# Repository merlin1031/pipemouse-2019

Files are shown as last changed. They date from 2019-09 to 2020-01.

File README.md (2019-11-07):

# pipemouse-2019
Tiny FPV Rover for Pipes
Was ist "PipeMouse 2019"? im Prinzip ist das ein kleiner FPV-Rover mit Kettenantrieb, der klein genug ist um in Röhren oder Schächten bewegt werden zu können. Durch den Antrieb mittels Ketten soll es den Rover möglich sein, auch über kleine Hindernisse oder Absätze zu fahren. Gesteuert wird das Modell mit einer handelsüblichen 2,4 GHz Fernsteuerung. Die Bildübertragung erfolgt über eine Miniatur-FPV-Kamera mit 5,8 GHz Funkübertragung.

## Idee und Konzept
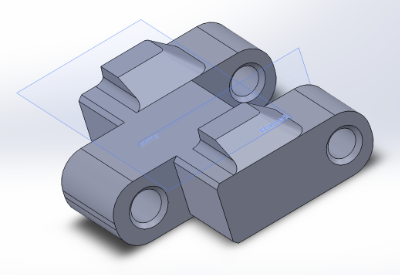
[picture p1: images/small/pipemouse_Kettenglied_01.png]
PipeMouse 2019 - Einzelnes Kettenglied

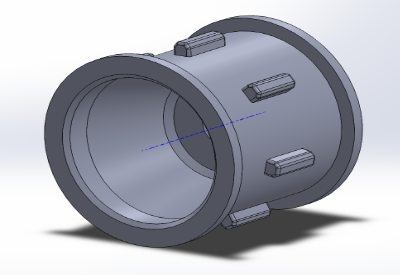
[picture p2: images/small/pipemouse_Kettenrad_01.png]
PipeMouse 2019 - Kettenrad

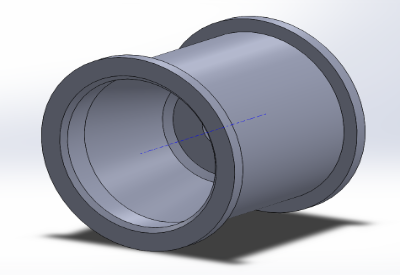
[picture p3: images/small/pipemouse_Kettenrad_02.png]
PipeMouse 2019 - Laufrad zur Unterstüzung der Laufkette

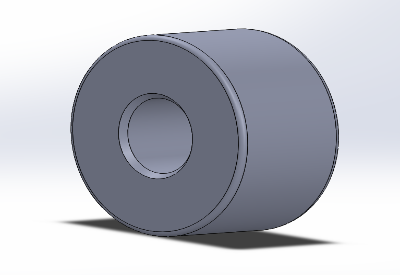
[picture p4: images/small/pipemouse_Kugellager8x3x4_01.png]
PipeMouse 2019 - Kugellager 8x3x4 für die Laufräder


Altenativer Ansatz für Kette mit Gummi-Pads. Aus Moosgummi werden die Pads gelasert und mit Kontaktkleber (z.B. Uhu Por oder Pattex auf den einzelnen Kettengliedern aufgeklebt).
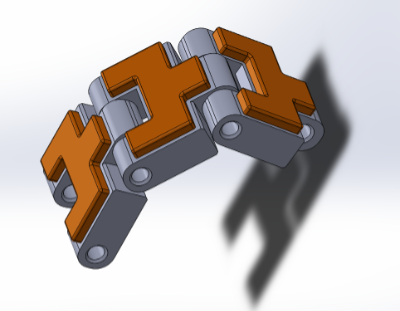
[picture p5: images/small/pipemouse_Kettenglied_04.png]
PipeMouse 2019 - Simulation Kettenglieder mit Gummi-Pad

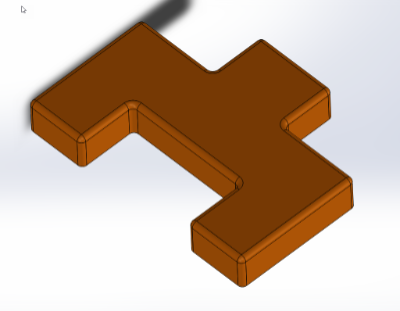
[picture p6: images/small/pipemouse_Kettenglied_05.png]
PipeMouse 2019 - Gummi-Pad für Kettenglied

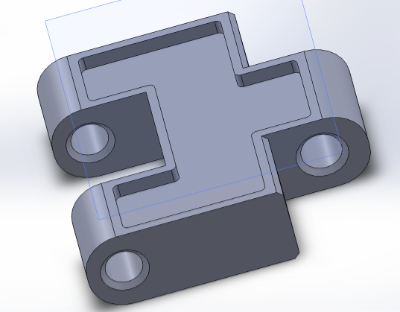
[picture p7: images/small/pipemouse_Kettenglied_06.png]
PipeMouse 2019 - Aussparung für Gummi-Pad in Kettenglied


## Komponenten und Bauteile
### Antrieb
Der Antrieb erfolgt durch zwei auf 360°-Betrieb umgebaute Mini-Servos der 8g-Klasse. Dadurch wird kein besonderer ESC für die Steuerung des Rovers benötigt. Die Steuerung von linker und rechter Kettenseite kann über einem in der Fernsteuerung progammierten Mischer erfolgen.
### Kettenstrang
Der Kettenstrang wird im 3D-Drucker aus PLA gedruckt. Als Verbinger zwischen den einzelnen Kettengliedern kommen PLA-Reste mit einem Durchmesser von 1,75mm zum Einsatz. Widerhaken auf der Lauffläche den Kettengliedern ermöglichen einen sicheren Vortrieb auf rauhen Untergründen, oder an steilen Absätzen. Auf sehr glatten Untergründen werden sicherlich Probleme mit dem Vortrieb auftreten, was aber vernachlässigbar sein dürfte, da in der Wettbewerbs-Arena geeignete Werkstoffe als Fahruntergrund vorhanden sein werden.
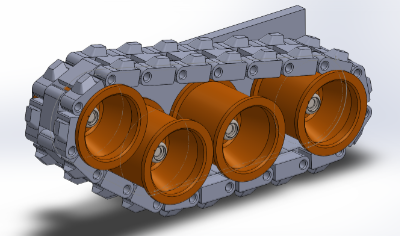
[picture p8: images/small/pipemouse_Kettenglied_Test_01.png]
PipeMouse 2019 - Test Kette mit Baugruppenfeature Riemen/Kette (Aussenansicht)

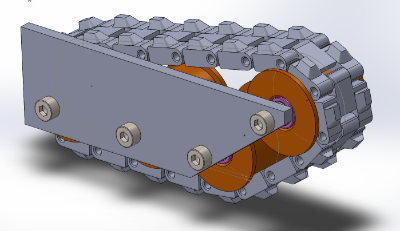
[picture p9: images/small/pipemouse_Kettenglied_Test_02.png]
PipeMouse 2019 - Test Kette mit Baugruppenfeature Riemen/Kette (Innenansicht)

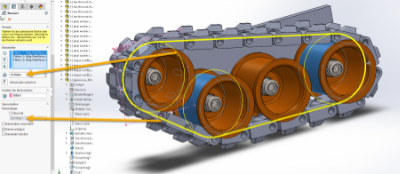
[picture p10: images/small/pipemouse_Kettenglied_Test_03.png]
PipeMouse 2019 - Test Kette mit Baugruppenfeature Riemen/Kette (Feature-Einstellungen)


Zeichungen von Kettenglied und Kettenrad ligen als PDF-Zeichnung im Verzeichnis /CAD/

### Fahrzeugwanne
Die Fahrzeugwanne dient der Aufnahme der Laufräder und der Antriebs-Servos. Sie wird so gestaltet sein, dass sie möglichst viel Bodenfreiheit und eine Möglichkeit der Kettenspannung bieten wird.
### Steuerung
Gesteuert wird der Rover mittels einer handelsüblichen Funkfernsteuerung mit 2,4 GHz-Technologie. In diesem speziellen Fall wird ein Exemplar der Firma FrySky (Taranis) zum Einsatz kommen. Diese Fernsteuerung bietet die Möglichkeit, die eingesetzte Open-Sorce Firmware eigenständig upzudaten und bietet umfangreiche Möglichkeiten der eingenen Programmierung. Zudem sind sehr günstige Miniatur-Empfänger in Briefmarken-Größe verfügbar.
### Stromversorgung
Als Stromquelle dient dem Rover ein 2S 450mAh Lipo-Akku, der aus der Tiny Whoop Copter Szene stammt. Der Vorteil dieses Akkus besteht darin, das die Einzelzellen recht schmal und klein gebaut sind und dadurch sehr wenig Platz im Rover benötigen.

## weitere Infos

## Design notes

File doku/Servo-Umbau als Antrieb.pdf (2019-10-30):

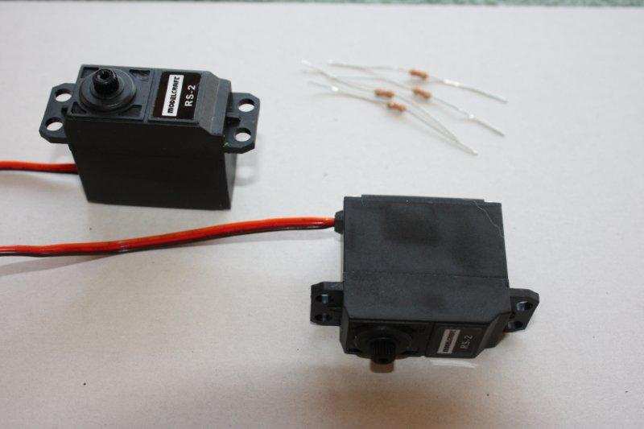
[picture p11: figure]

Seite 1 von 8

Servo-Umbau, damit er als Antrieb verwendet werden kann

Hallo Zusammen,

Ich möchte Euch mal Anhand eines Beispiels zeigen, wie man einen Servo zu einem Antrieb ohne Endstellung umbauen kann und somit als Antrieb für z.B. eine Bruder-Raupe verwenden kann.

Material:

### 1 Stück Standardservo von Conrad Nr. 205111 – 62 2 Stück Metallfilm-Widerstand, axial bedrahtet, Bauform0207, 2,4kOhm, 0.25Watt

von Conrad Nr. 409480-62 (Achtung Art. Nr. ist für ein 100er Pack)

Es ist WICHTIG, dass man wirklich 2,4kOhm Widerstände verwendet, denn bei kleineren Widerständen, z.B. 2,2kOhm ist der Nullpunkt vom Servo nicht so genau und man muss öfters mit der Trimmung den Servo zum Stillstand bringen.
Hier mal das benötigte Material im Überblick:

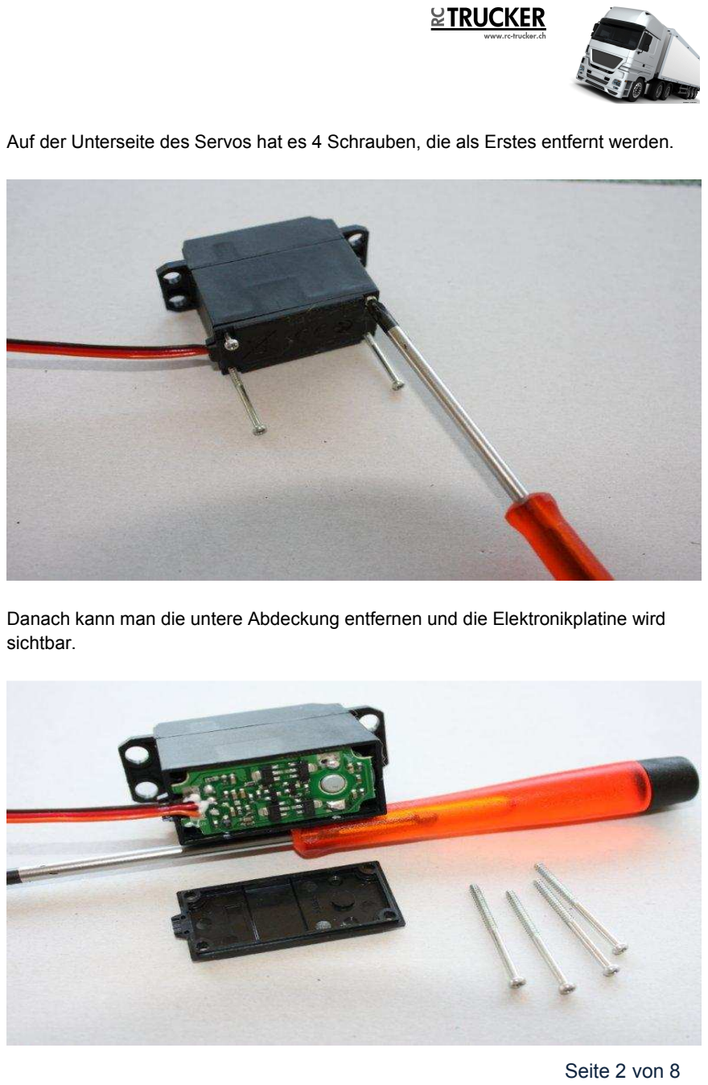
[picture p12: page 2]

Seite 2 von 8

Auf der Unterseite des Servos hat es 4 Schrauben, die als Erstes entfernt werden.

Danach kann man die untere Abdeckung entfernen und die Elektronikplatine wird sichtbar.

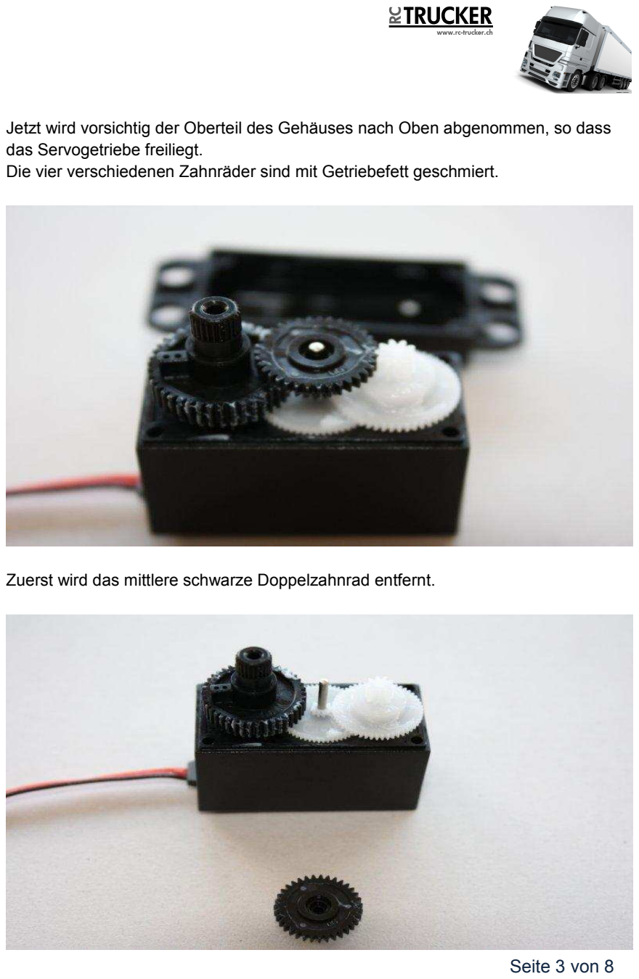
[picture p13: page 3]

Seite 3 von 8

Jetzt wird vorsichtig der Oberteil des Gehäuses nach Oben abgenommen, so dass das Servogetriebe freiliegt.
Die vier verschiedenen Zahnräder sind mit Getriebefett geschmiert.

Zuerst wird das mittlere schwarze Doppelzahnrad entfernt.

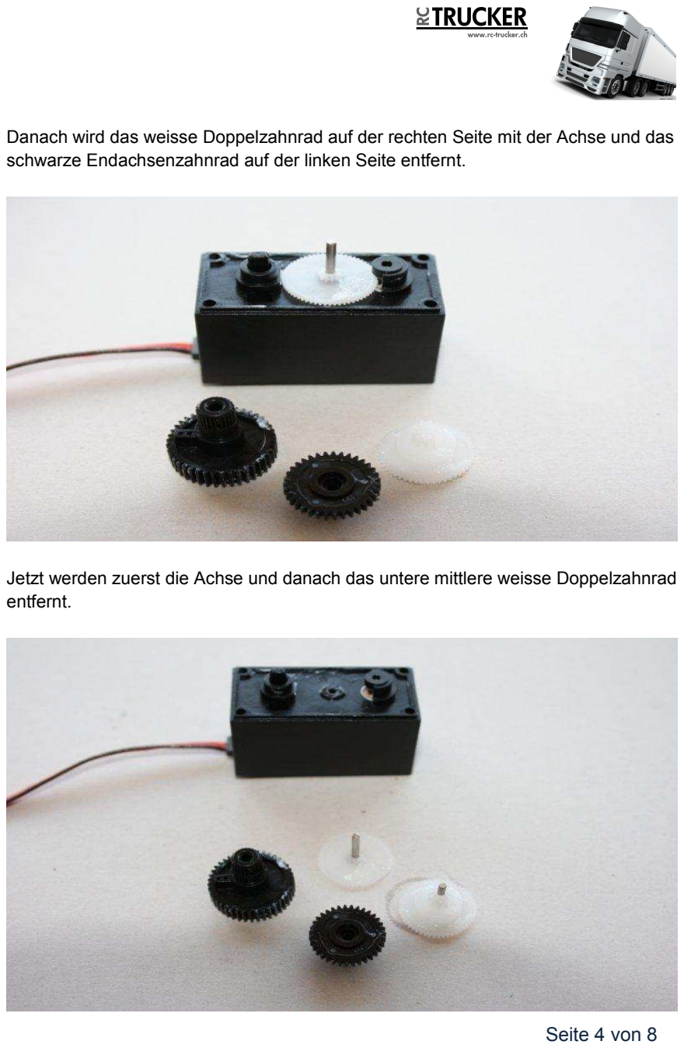
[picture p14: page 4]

Seite 4 von 8

Danach wird das weisse Doppelzahnrad auf der rechten Seite mit der Achse und das schwarze Endachsenzahnrad auf der linken Seite entfernt.

Jetzt werden zuerst die Achse und danach das untere mittlere weisse Doppelzahnrad entfernt.

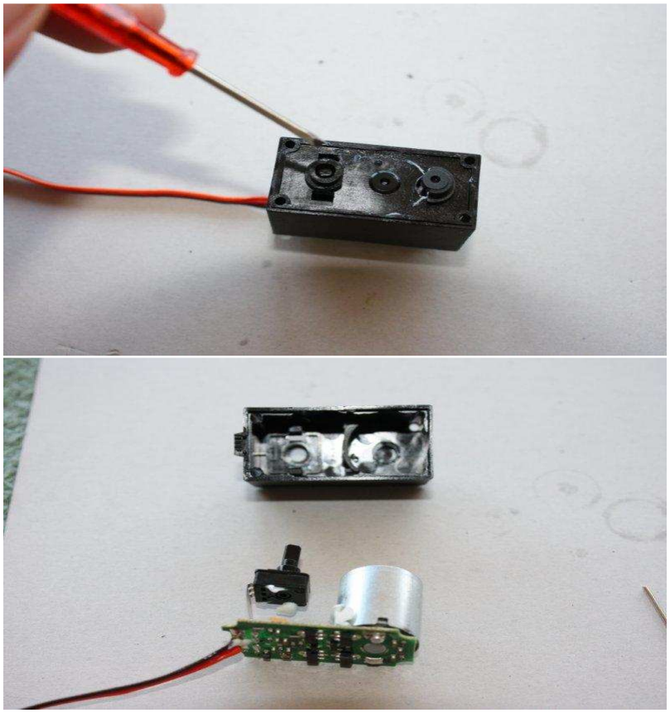
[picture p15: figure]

Seite 5 von 8

Jetzt wird die Elektronik ausgebaut. Dazu kann man VORSICHTIG mit einem kleinen Schraubendreher von Oben in die zwei kleinen Schlitze fahren und die Kunststoffklammern, die das Poti im Gehäuse halten, zur Seite drücken und die Elektronikplatine von unten aus dem Gehäuse ziehen.

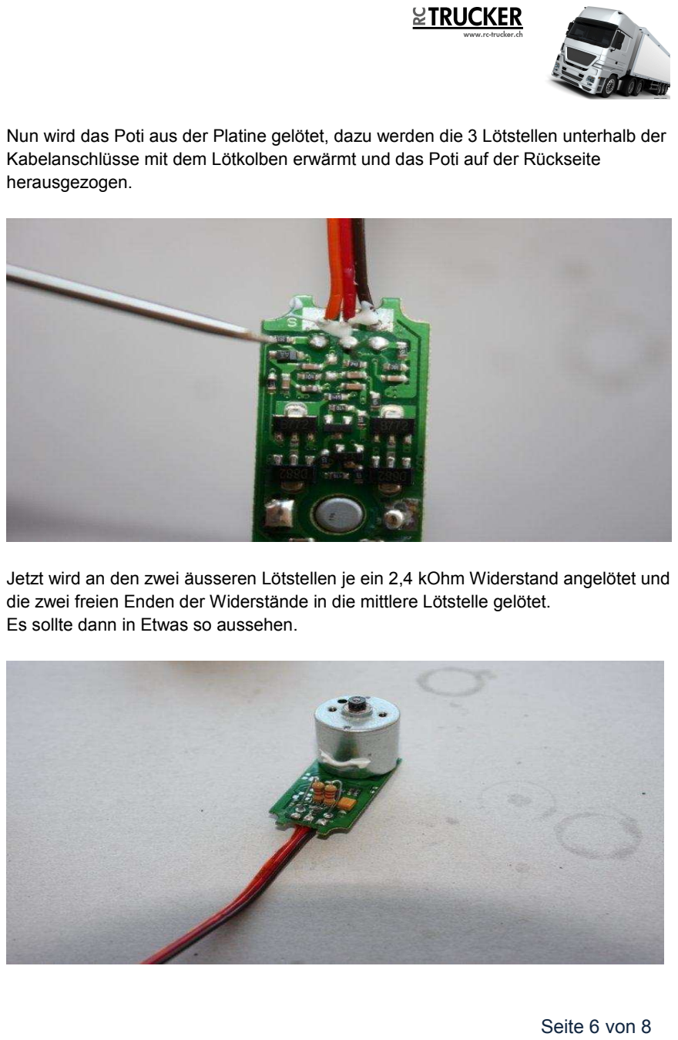
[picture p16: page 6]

Seite 6 von 8

Nun wird das Poti aus der Platine gelötet, dazu werden die 3 Lötstellen unterhalb der Kabelanschlüsse mit dem Lötkolben erwärmt und das Poti auf der Rückseite herausgezogen.

Jetzt wird an den zwei äusseren Lötstellen je ein 2,4 kOhm Widerstand angelötet und die zwei freien Enden der Widerstände in die mittlere Lötstelle gelötet.
Es sollte dann in Etwas so aussehen.

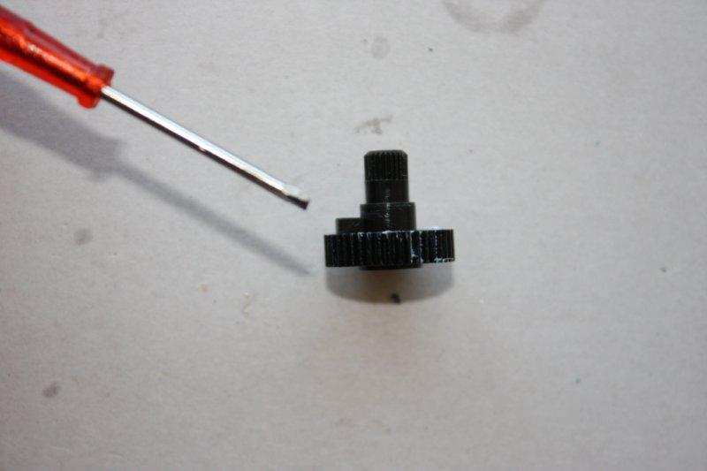
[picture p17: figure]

Seite 7 von 8

Jetzt wird am schwarzen Endachsenzahnrad noch der mechanische Anschlag entfernt.
Dazu benötigen wir ein Skalpell mit einer scharfen Klinge, wenn wir ein Feile dazu verwenden würden, würde auch die Oberfläche das Zahnrades aufgeraut und dadurch der Leichtlauf des Zahnrades beeinträchtigt.
Mit dem Skalpell wird entlang der Achse und der Zahnradfläche eingeschnitten, bis der Mechanische Anschlag entfernt ist. Es muss darauf geachtet werden, dass wirklich alles schön plan abgeschnitten ist, damit keine unnötige Reibung entsteht.

Vorher:

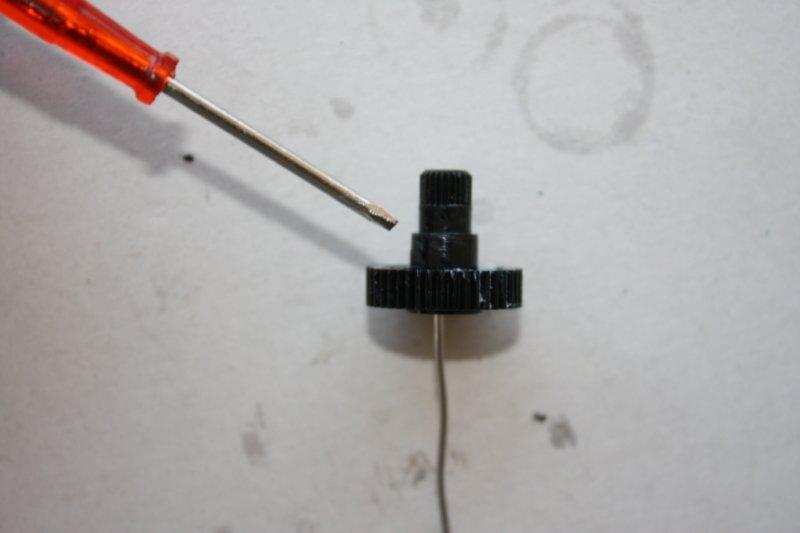
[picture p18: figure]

Seite 8 von 8

Danach:

Somit sind die Umbauarbeiten fertig und der Servo kann wieder zusammengebaut werden.
Schritt 1: die Elektronik in das Gehäuse schieben
Schritt 2: das untere mittlere weisse Doppelzahnrad einbauen und mit der Achse befestigen
Schritt 3: das schwarze Endachsenzahnrad auf der linken Seite und danach das weisse Doppelzahnrad auf der rechten Seite mit der Achse befestigen.
Schritt 4: das mittlere schwarze Doppelzahnrad einbauen
Schritt 5: jetzt wird vorsichtig der Oberteil des Gehäuses auf das Getriebe gesetzt. Schritt 6: die untere Abdeckung einsetzten und das ganze Gehäuse mit den vier Schrauben zusammenschrauben.

Viel Spass beim Nachbauen
Gruss Andreas

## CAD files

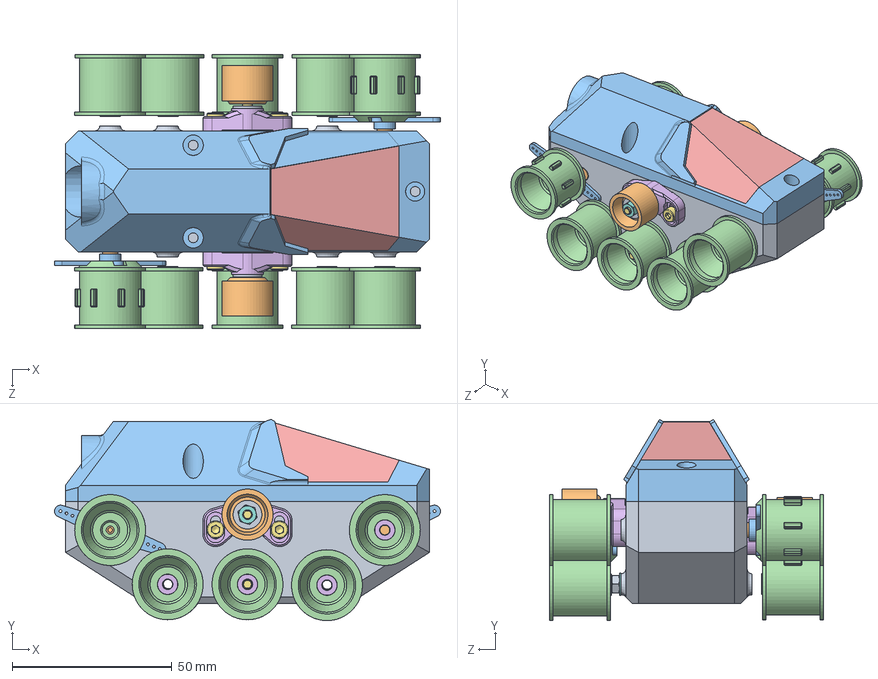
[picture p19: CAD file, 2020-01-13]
CAD/bg_PipeMouse_Bodenwanne.SLDASM
120.9 x 63.0 x 85.9 mm
pipemouse_Bodenwanne
pipemouse_Servo_SG90 x 2
pipemouse_Servohorn_SG90 x 2
pipemouse_KettenRad_v3 x 10
pipemouse_Kugellager_8x3x4 x 10
pipemouse_U-Scheibe x 16
socket head cap screw_iso
plain washer normal grade a_iso
hex nut style 1 gradeab_iso
Lipo_HappyModell_2S_300mAh
pipemouse_WannenDeckel
cadxx_Turbo_Eon
pipemouse_Deckel
pipemouse_KettenspannerBlock x 2
socket head cap screw_din x 6
hex nut style 1 gradeab_din x 4
plain washer large_din x 4
pipemouse_KettenspannRad x 2

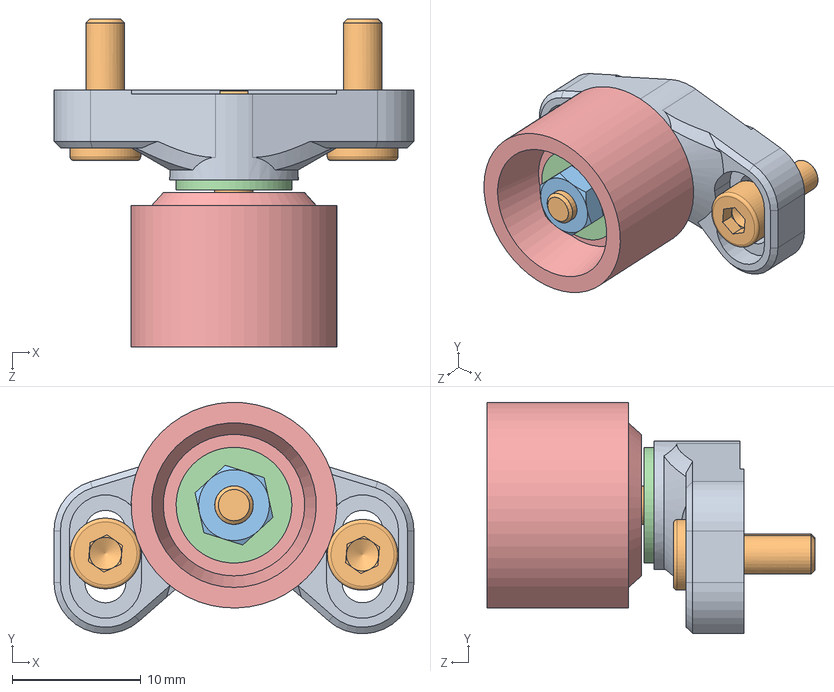
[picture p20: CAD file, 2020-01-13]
CAD/bg_Kettenspanner.SLDASM
28.0 x 18.0 x 25.5 mm
pipemouse_KettenspannerBlock
socket head cap screw_din x 3
hex nut style 1 gradeab_din x 2
plain washer large_din x 2
pipemouse_KettenspannRad
pipemouse_Kugellager_8x3x4

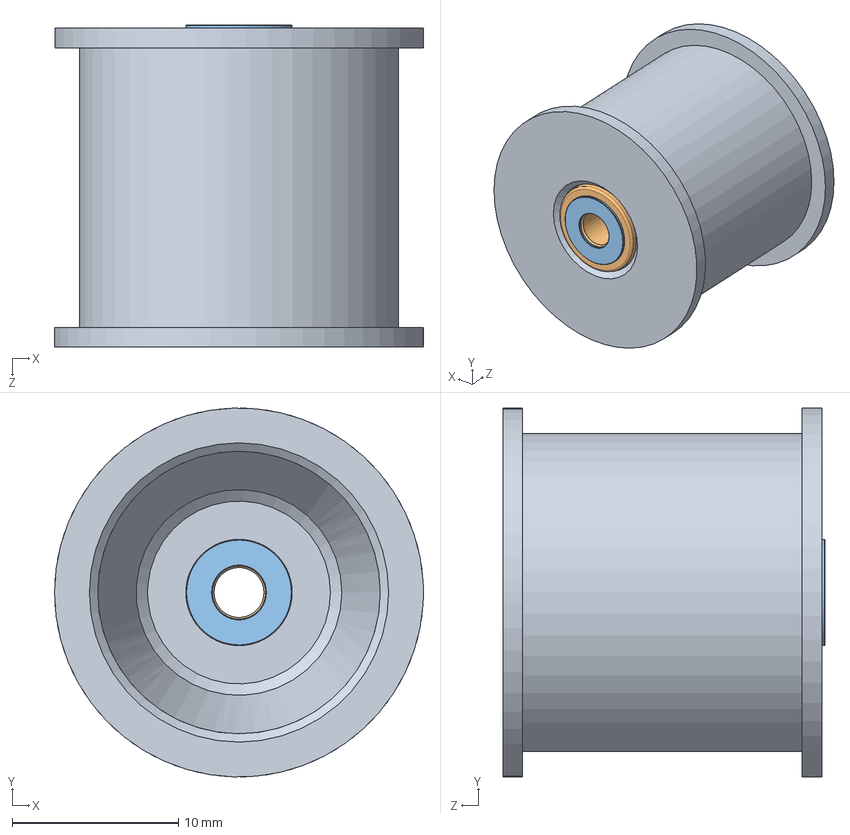
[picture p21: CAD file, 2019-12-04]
CAD/bg_PipeMouse_Laufrad.SLDASM
22.2 x 22.2 x 19.4 mm
pipemouse_KettenRad_v3
pipemouse_Kugellager_8x3x4
pipemouse_U-Scheibe x 2

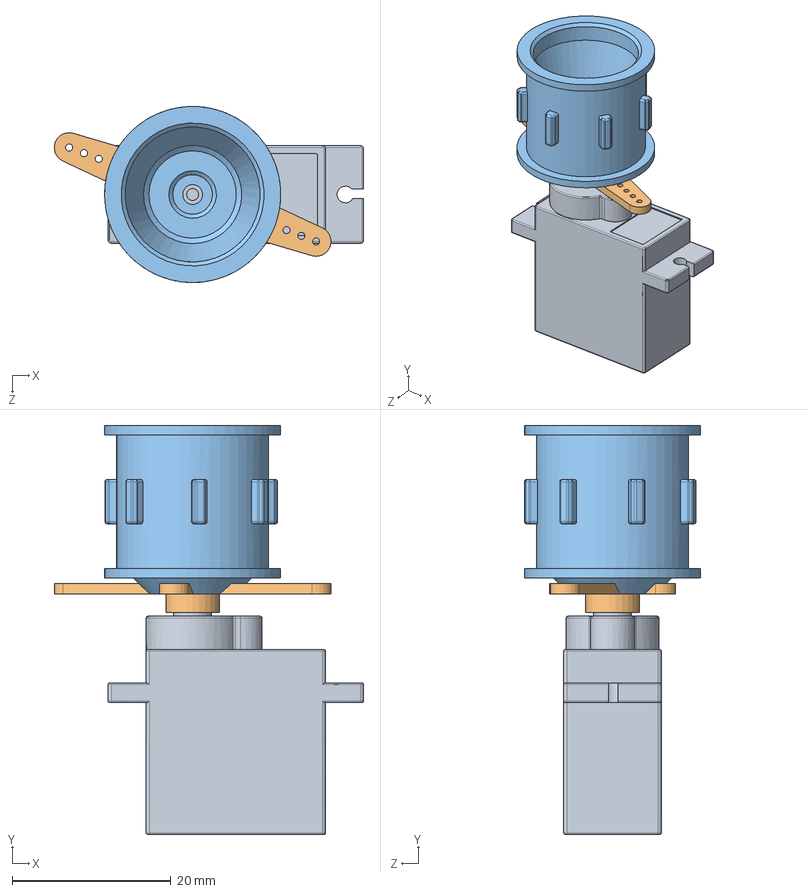
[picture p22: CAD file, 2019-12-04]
CAD/bg_PipeMouse_Antriebsstrang.SLDASM
39.0 x 51.5 x 22.2 mm
pipemouse_Servo_SG90
pipemouse_Servohorn_SG90
pipemouse_KettenRad_v3

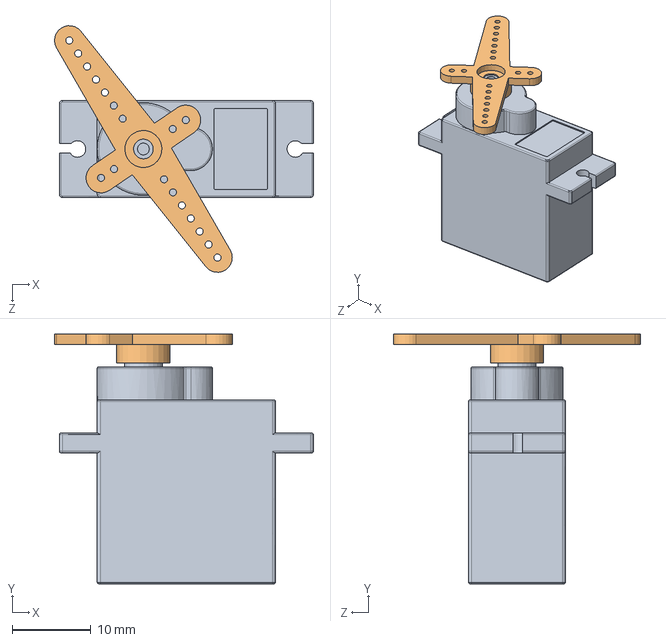
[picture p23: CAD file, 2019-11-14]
CAD/BG_PipeMouse_Servo_SG90.SLDASM
32.8 x 31.6 x 31.2 mm
pipemouse_Servo_SG90
pipemouse_Servohorn_SG90

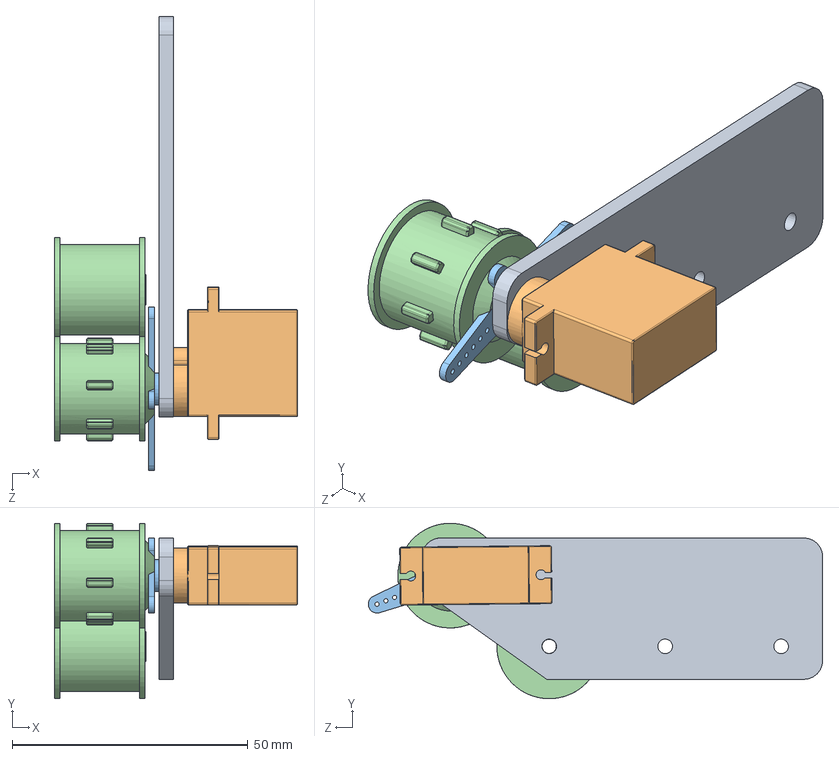
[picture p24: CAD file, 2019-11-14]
CAD/bg_PipeMouse_AntriebsTest.SLDASM
51.5 x 37.2 x 96.4 mm
pipemouse_KettenRäderAbstandsTest
pipemouse_Servo_SG90
pipemouse_Servohorn_SG90
pipemouse_KettenRad_v3 x 2
pipemouse_Kugellager_8x3x4
pipemouse_U-Scheibe x 2

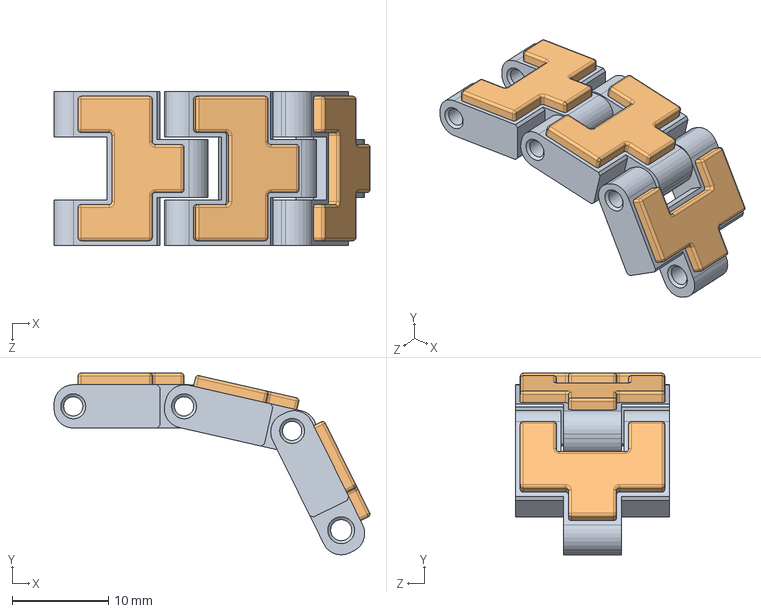
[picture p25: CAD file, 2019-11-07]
CAD/bg_PipeMouse_SimulationGummiKette.SLDASM
32.8 x 18.9 x 16.0 mm
pipemouse_Kettenglied x 3
pipemouse_GummiPlatte x 3

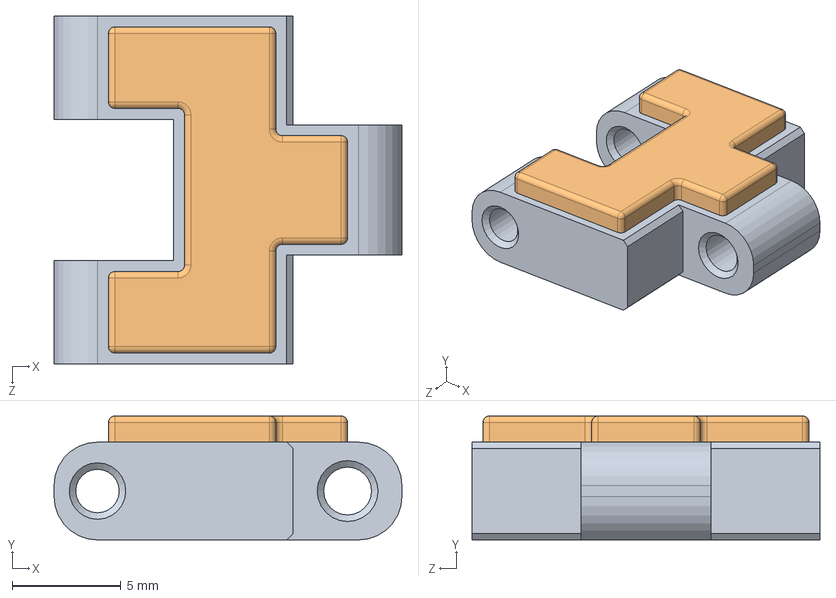
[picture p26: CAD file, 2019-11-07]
CAD/bg_PipeMouse_KettenGliedGummi.SLDASM
16.0 x 5.70 x 16.0 mm
pipemouse_Kettenglied
pipemouse_GummiPlatte

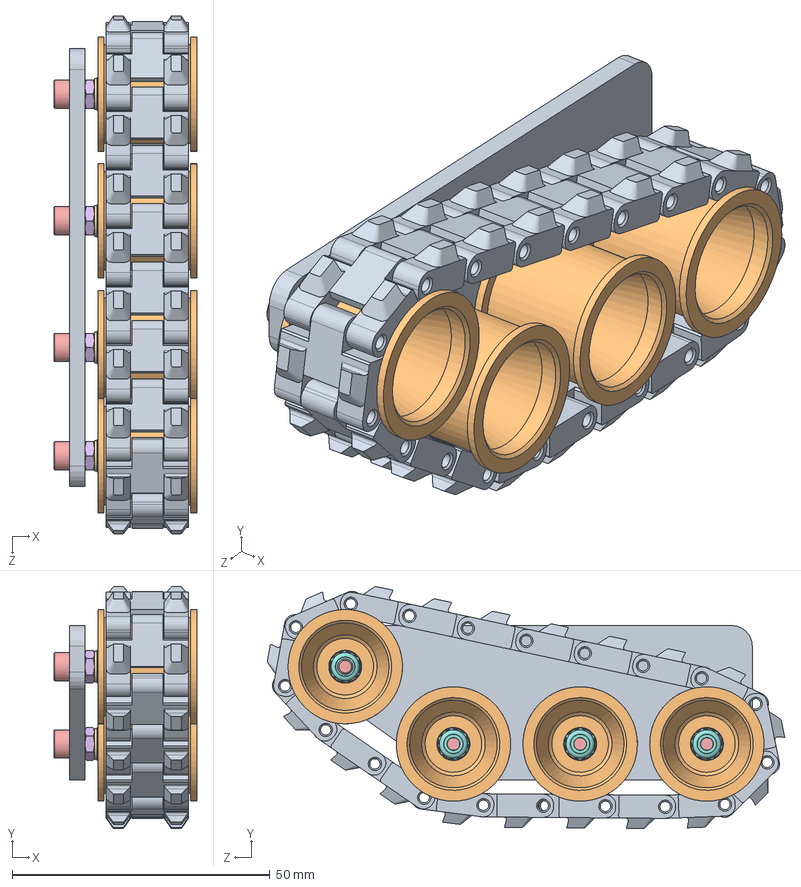
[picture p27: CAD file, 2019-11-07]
CAD/bg_PipeMouse_RäderTest.SLDASM
27.7 x 47.0 x 100.4 mm
pipemouse_KettenRäderAbstandsTest
pipemouse_KettenRad_v3 x 4
pipemouse_Kugellager_8x3x4 x 4
pipemouse_U-Scheibe x 8
socket head cap screw_iso x 4
hex thin nut chamfered gradeab_iso x 4
plain washer small grade a_iso x 8
torque nut 08_iso x 4
pipemouse_Kettenglied x 19

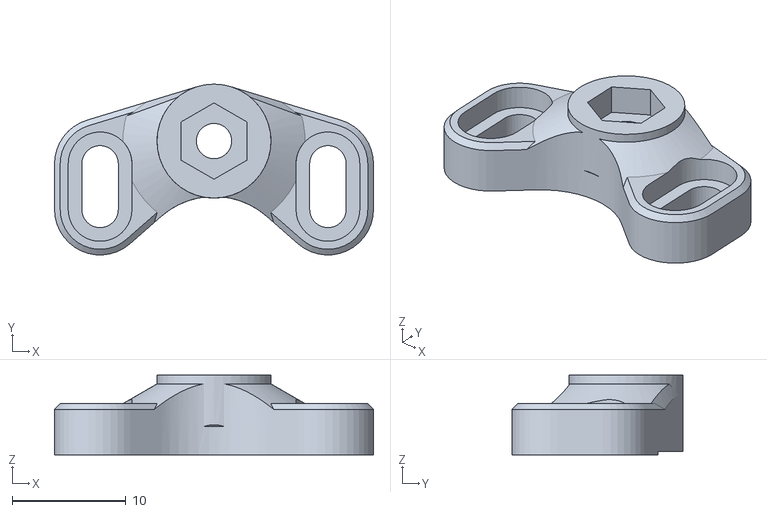
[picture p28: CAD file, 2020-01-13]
CAD/3D-Druck-Modelle/pipemouse_KettenspannerBlock.STL
28.0 x 15.0 x 7.00

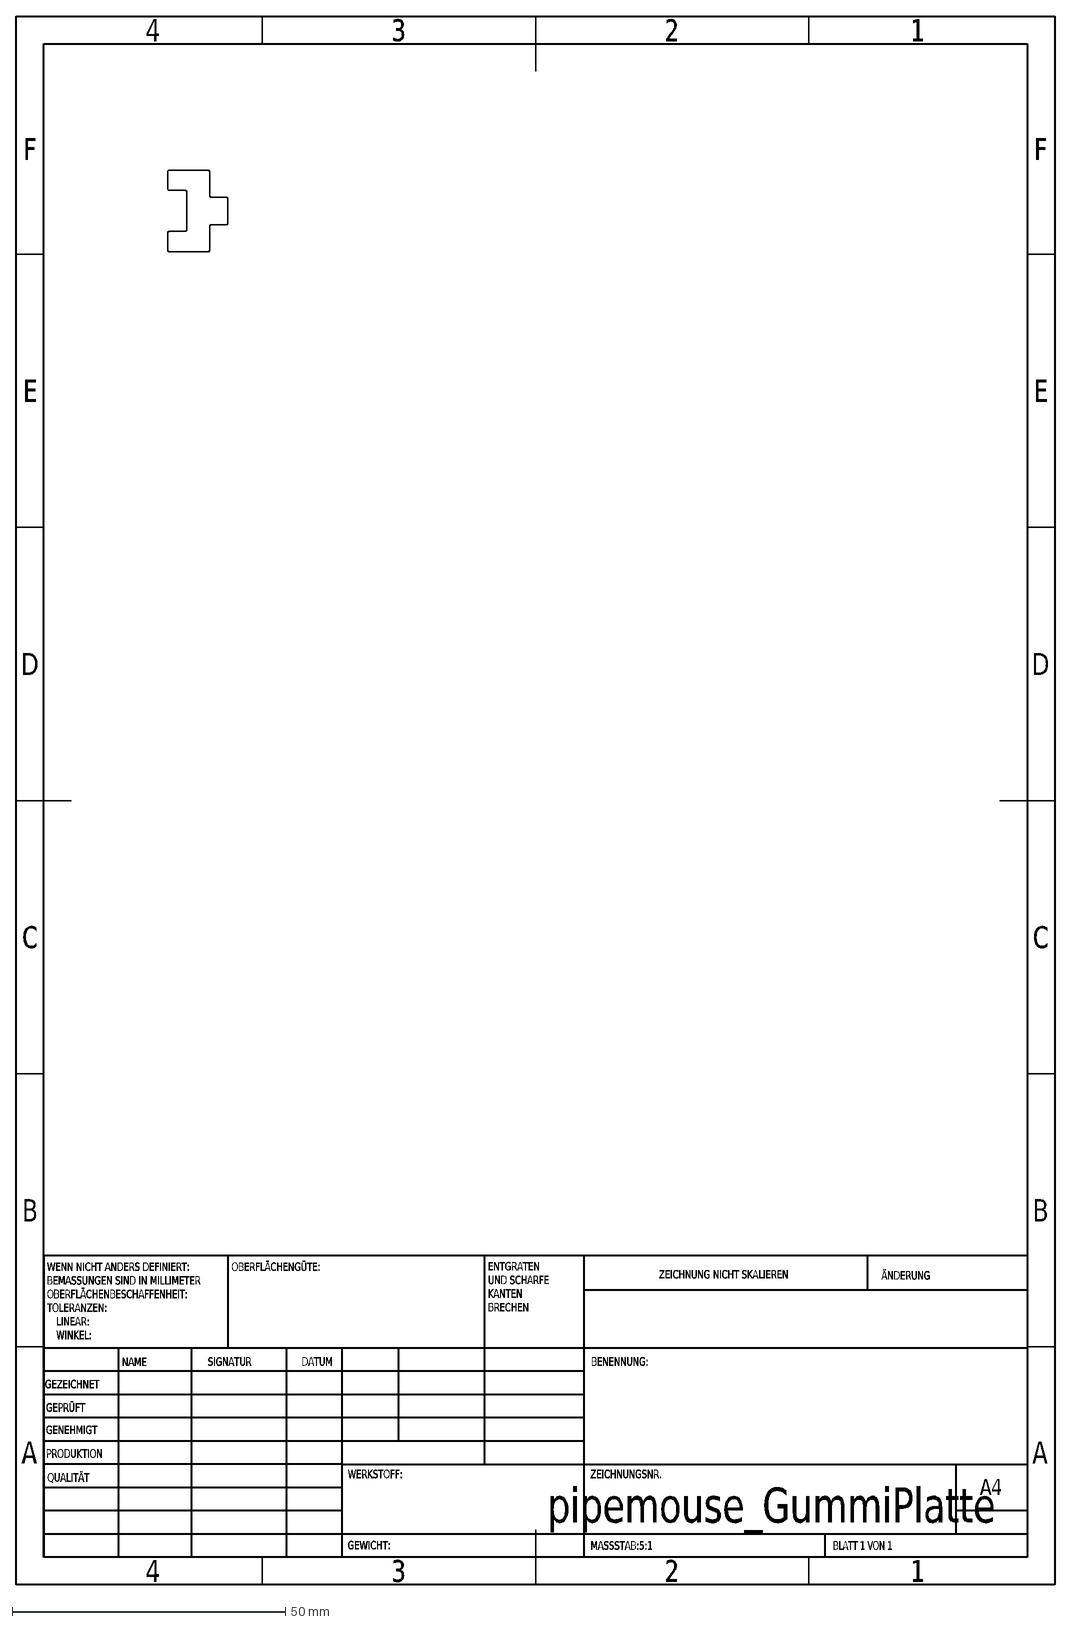
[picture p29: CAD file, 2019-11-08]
CAD/Laser-Daten/pipemouse_GummiPlatte.DXF
A
B
C
D
E
F
4
3
2
1
pipemouse_GummiPlatte
GEWICHT:
A4
BLATT 1 VON 1
MASSSTAB:5:1
ZEICHNUNGSNR.
BENENNUNG:
ÄNDERUNG
ZEICHNUNG NICHT SKALIEREN
WERKSTOFF:
DATUM
SIGNATUR
NAME
ENTGRATEN
UND SCHARFE
KANTEN
BRECHEN
OBERFLÄCHENGÜTE:
WENN NICHT ANDERS DEFINIERT:
BEMASSUNGEN SIND IN MILLIMETER
OBERFLÄCHENBESCHAFFENHEIT:
TOLERANZEN:
LINEAR:
WINKEL:
QUALITÄT
PRODUKTION
GENEHMIGT
GEPRÜFT
GEZEICHNET

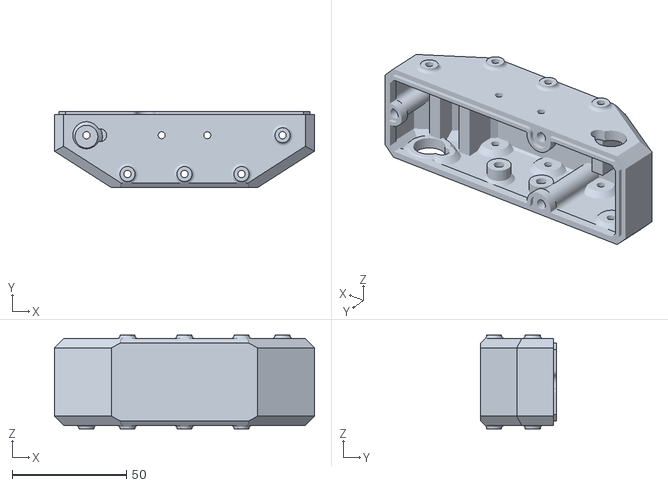
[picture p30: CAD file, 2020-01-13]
CAD/3D-Druck-Modelle/pipemouse_Bodenwanne.STL
114.0 x 33.5 x 41.0

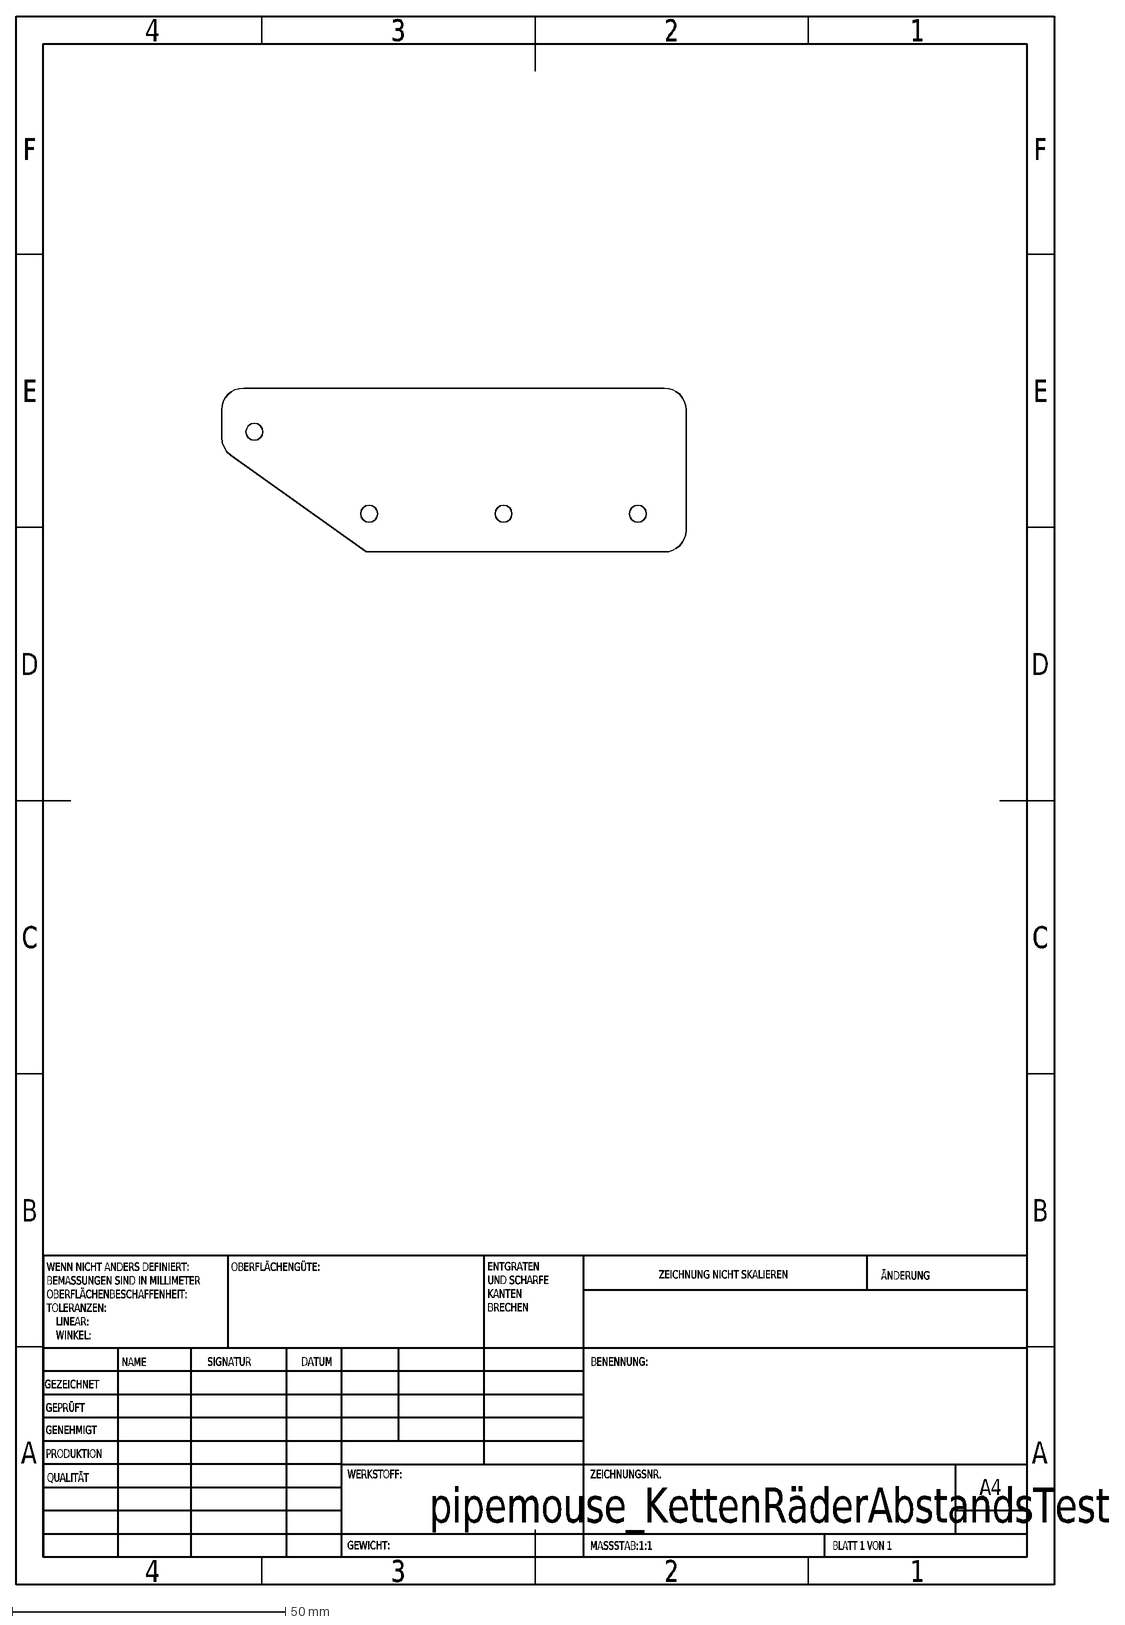
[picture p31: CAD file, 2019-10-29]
CAD/Laser-Daten/pipemouse_KettenRäderAbstandsTest.DXF
A
B
C
D
E
F
4
3
2
1
pipemouse_KettenRäderAbstandsTest
GEWICHT:
A4
BLATT 1 VON 1
MASSSTAB:1:1
ZEICHNUNGSNR.
BENENNUNG:
ÄNDERUNG
ZEICHNUNG NICHT SKALIEREN
WERKSTOFF:
DATUM
SIGNATUR
NAME
ENTGRATEN
UND SCHARFE
KANTEN
BRECHEN
OBERFLÄCHENGÜTE:
WENN NICHT ANDERS DEFINIERT:
BEMASSUNGEN SIND IN MILLIMETER
OBERFLÄCHENBESCHAFFENHEIT:
TOLERANZEN:
LINEAR:
WINKEL:
QUALITÄT
PRODUKTION
GENEHMIGT
GEPRÜFT
GEZEICHNET

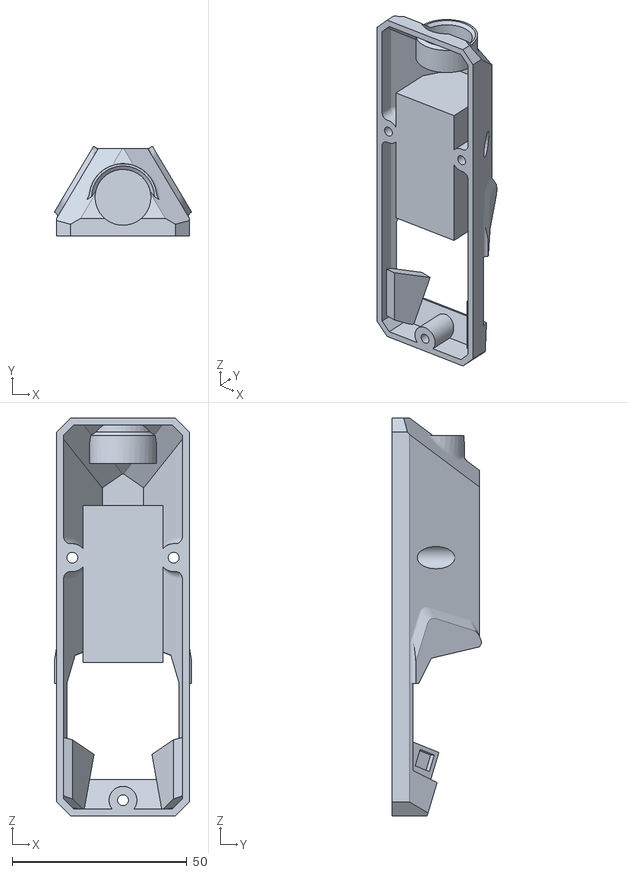
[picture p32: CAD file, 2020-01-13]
CAD/3D-Druck-Modelle/pipemouse_WannenDeckel.STL
39.4 x 25.6 x 114.0

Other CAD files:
CAD/pipemouse_KettenspannerBlock.SLDPRT
CAD/3D-Druck-Modelle/pipemouse_GummiPlatte.STL
CAD/pipemouse_KettenspannRad.SLDPRT
CAD/3D-Druck-Modelle/pipemouse_Kettenglied_GummiPad.STL
CAD/Laser-Daten/Laser_GummiPad.3dm
CAD/Laser-Daten/pipemouse_KettenRäderAbstandsTest.3dm
CAD/Lipo_HappyModell_2S_300mAh.SLDPRT
CAD/Scheibe.SLDPRT
CAD/Scheibe.STL
CAD/bg_PipeMouse_RäderTest.SLDDRW
CAD/cadxx_Turbo_Eon.SLDPRT
CAD/pipemouse_AkkuKlappe.sldprt
CAD/pipemouse_Bodenwanne.SLDPRT
CAD/pipemouse_Deckel.sldprt
CAD/pipemouse_GummiPlatte.SLDDRW
CAD/pipemouse_GummiPlatte.SLDPRT
CAD/pipemouse_KettenRad_v3.SLDDRW
CAD/pipemouse_KettenRad_v3.SLDPRT
CAD/pipemouse_KettenRad_v3.STL
CAD/pipemouse_KettenRäderAbstandsTest.SLDDRW
CAD/pipemouse_KettenRäderAbstandsTest.SLDPRT
CAD/pipemouse_Kettenglied.SLDDRW
CAD/pipemouse_Kettenglied.SLDPRT
CAD/pipemouse_Kugellager_8x3x4.SLDPRT
CAD/pipemouse_Servo_SG90.SLDPRT
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

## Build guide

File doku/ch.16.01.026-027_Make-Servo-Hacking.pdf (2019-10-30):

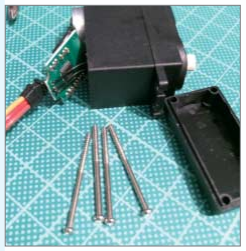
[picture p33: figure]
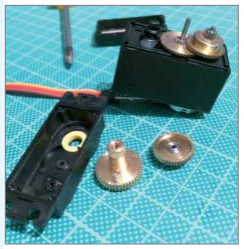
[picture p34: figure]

26| Make: 1/2016

Einfache Modellbauservos gibt es schon für ein paar Euro im Internet zu kaufen. Die Entwicklungswerkzeuge für Arduino und Co. enthalten bereits im Standardumfang Bibliotheken, mit deren Hilfe die Steuerung von Servos einfach möglich ist. Weitere Elektronik wie zum Beispiel ein Motortreiber wird nicht benötigt, da der Ausgang des Chips, der die Ansteuerung übernimmt, nicht belastet wird.
Servos sind also günstig zu haben und leicht anzusteuern, aber leider ein wenig beschränkt. Die Servowelle hat häufig nur einen Drehwinkel von 180 Grad, dann ist konstruktionsbedingt zunächst Schluss. Mit ein paar Handgriffen kann man verschiedene Servotypen aber auf Dauerrotation um -bauen. Damit werden Servos zu langsamen, aber günstigen Motoren.
Einem Servo wird mittels eines puls -weitenmodulierten Signals (PWM) mitgeteilt, welche Position die Servowelle anfahren soll. Üblicherweise steckt die Welle im Servo -gehäuse auf einem Potentiometer, welches den Drehwinkel als Widerstandsverhältnis abbildet. Die im Servo eingebaute Elektronik vergleicht den Ansteuerimpuls (Soll) mit dem aktuellen Drehwinkel (Ist) und dreht so lange an der Welle, bis Drehwinkel und Eingangsimpuls übereinstimmen.
Trennt man die mechanische Verbindung zwischen Poti und Welle und stellt das Widerstandsverhältnis fest auf „Mitte“ ein, so steht das Servo bei einem Impuls für den Drehwinkel 90 Grad still. Bei einem Signal für 0 Grad beginnt das Servo gegen den Uhrzeigersinn zu laufen, bei einem Signal für 180 Grad mit dem Uhrzeigersinn. Durch die Trennung vom Poti verändert sich während der Drehung das Widerstandsverhältnis nicht, sodass die Servoelektronik meint, weiter auf den geforderten Wert zusteuern zu müssen. Je nach Servotyp stehen der Endlosrotation aber noch mechanische Hürden entgegen, die entfernt werden müssen, bevor das Servo durchdrehen kann.

# SERVO-HACKING |

# Ein Servo dreht durch

### Modellbauservos sind günstige, kleine Getriebemotoren, die jedoch

in der Regel nur um einen bestimmten Winkel rotieren können.

### Mit einem kleinen Eingriff werden sie zu kontinuierlich drehenden

Antriebsmotoren, zum Beispiel für Roboter.

von Joachim Haas

## Kurzinfo

Zeitaufwand:
rund 20 Minuten

Kosten:
ab 5 Euro

Löten:
Grundkenntnisse Entlöten
und Löten

Feinwerkzeug:
Kreuz-Schraubendreher,
Seitenschneider, Flachzange

## Material

»Modellbauservo
»zwei identische Widerstände

Schwierigkeitsgrad

leicht | schwer

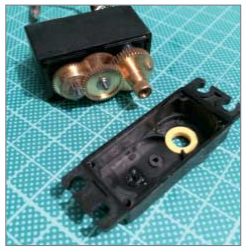
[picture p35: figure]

### 1 Servo öffnen und Deckel abnehmen

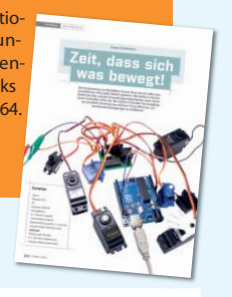
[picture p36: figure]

Vier Schrauben halten Boden, Gehäuse und Deckel. Beim Abnehmen des Bodens hat man zusammen mit der Anschlussleitung gleich die Platine mit der Steuerelektronik in der Hand. Typischerweise führen von dort zwei Drähte zum Motor, drei zum Potentiometer. Sind die vier Schrauben entfernt, ist auch der Deckel des Servos bereits lose. Er lässt sich ebenfalls leicht lösen. Unter dem Deckel befindet sich das Getriebe, das üblicherweise gut gefettet ist. Das Fett sollte man nicht unnötig abwischen.

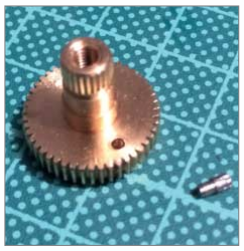
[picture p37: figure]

### 2 Sperre entfernen

Die Servowelle muss man aus zwei Gründen abnehmen. Zum einen muss man die mechanische Sperre, die eine volle Drehung verhindert, entfernen. Der Dorn ist eingepresst. Er lässt sich mit einer Flachzange greifen und unter leichtem Hin- und Herdrehen herausziehen. Außerdem kommt man so an das Poti heran. Bei Servos mit Kunststoffgetriebe ist die mechanische Sperre häufig ein Steg, der an die Servowelle angeformt ist. Dieser muss abgefeilt werden, möglichst ohne die Welle oder das Zahnrad zu beschädigen.

### SERVO-HOW-TO

Wie Servos funktionieren, steht in unserem Grundlagen-Artikel in c’t Hacks
1/2014 ab Seite 64.

© Copyright by Maker Media GmbH

Persönliches PDF für alle Leser der c't aus 30625 Hannover

Make: 1/2016 | 27

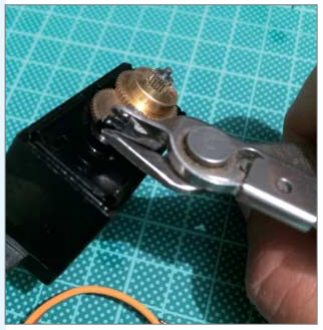
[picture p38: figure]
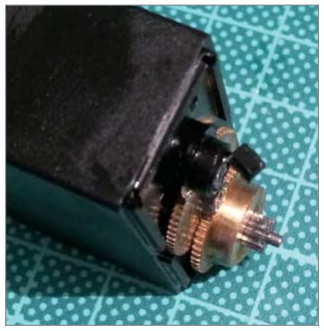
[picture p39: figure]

### 3 Poti mechanisch außer Gefecht setzen

Die Servowelle steckt auf dem Potentiometer, das die Postionsrückmeldung gibt. Das Poti muss nicht nur elektrisch außer Betrieb genommen werden (Widerstandsbrücke), sondern auch mechanisch, denn es lässt sich maximal um 270 Grad drehen. Also setzt man den Seitenschneider möglichst bündig an und knipst die Potiwelle ab. An der Ober -seite des Servos war es das mit den Arbeiten. Das Getriebe kann wieder zusammengesetzt und mit dem Deckel versehen werden. Dann verteilt sich bei den Arbeiten an der Unterseite auch nicht das Schmierfett aus dem Getriebe auf dem Arbeitsplatz.

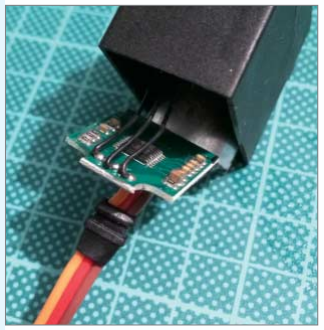
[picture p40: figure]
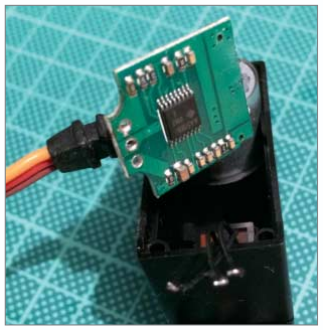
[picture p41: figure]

### 4 Poti elektrisch abklemmen

Die drei Drähte, die vom Poti kommen, schneidet man nun ab und lötet die Überreste aus.
(Als schnelle, aber unsicherere Alternative zur Wider standsbrücke könnte man das Poti auch im Servo belassen und nach dem Abschneiden der Achse einfach in Mittelstellung fixieren. Es ist allerdings möglich, dass es sich durch Vibrationen im Betrieb verstellt.)

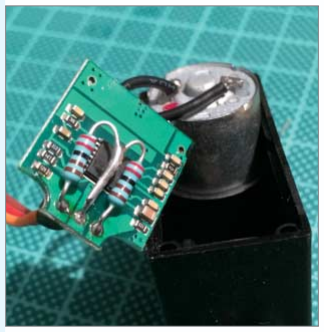
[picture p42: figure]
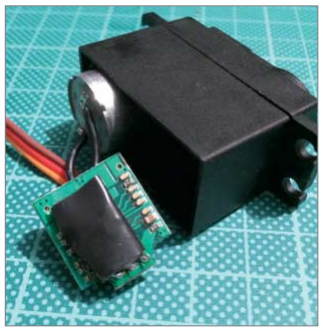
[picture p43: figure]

### 5 Widerstandsbrücke einlöten

In die beiden äußeren Lötaugen lötet man nun zwei exakt gleich große Widerstände ein, zum Beispiel 2,2 kOhm. Am besten nimmt man Metallschichtwiderstände mit geringeren Toleranzen und sucht vorher mit dem Ohmmeter ein identisches Widerstands-Paar heraus. Beide Widerstände lötet man dann am mittleren Lötauge an. Einfach einen von beiden durchstecken, das Beinchen des anderen kürzen, parallel legen und anlöten. Zur Sicherheit verpackt man die Widerstandsbrücke in Isolierband oder Schrumpfschlauch.

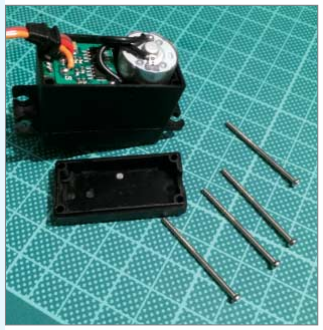
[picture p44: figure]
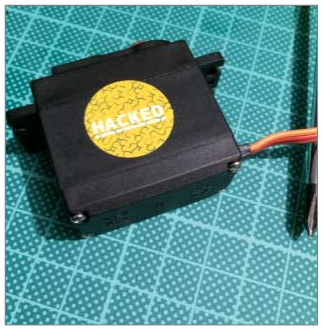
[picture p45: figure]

### 6 Zusammenbau

Nun noch alles wieder im Servogehäuse verstauen und zuschrauben. Um gehackte Servos nicht mit normalen Exemplaren zu verwechseln, hilft eine
kleine Kennzeichnung. | —phs

© Copyright by Maker Media GmbH

Persönliches PDF für alle Leser der c't aus 30625 Hannover

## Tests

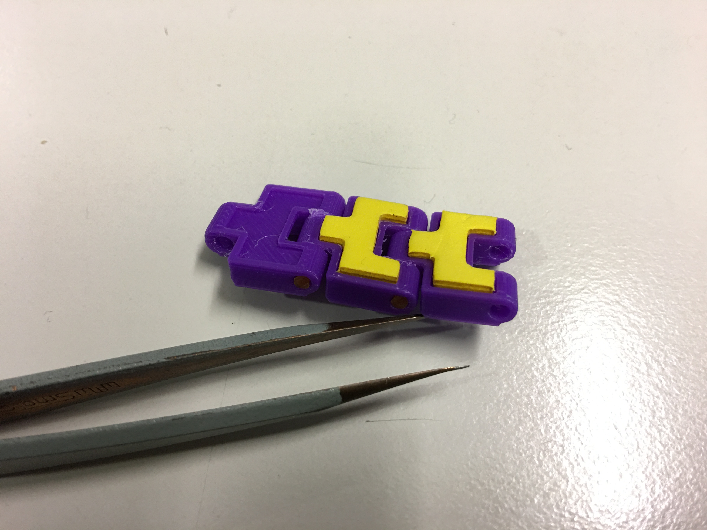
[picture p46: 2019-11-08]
images/Test_GummiPad02.jpg

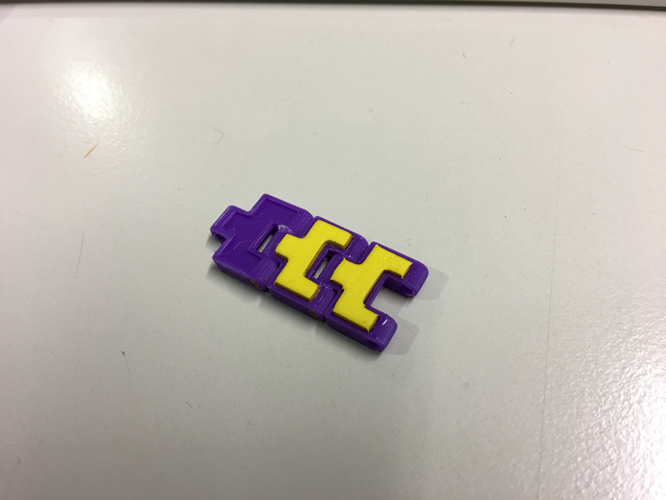
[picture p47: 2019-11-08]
images/Test_GummiPad_01.jpg

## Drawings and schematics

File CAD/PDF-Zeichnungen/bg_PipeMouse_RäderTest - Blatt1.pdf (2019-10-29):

E | E
F | F

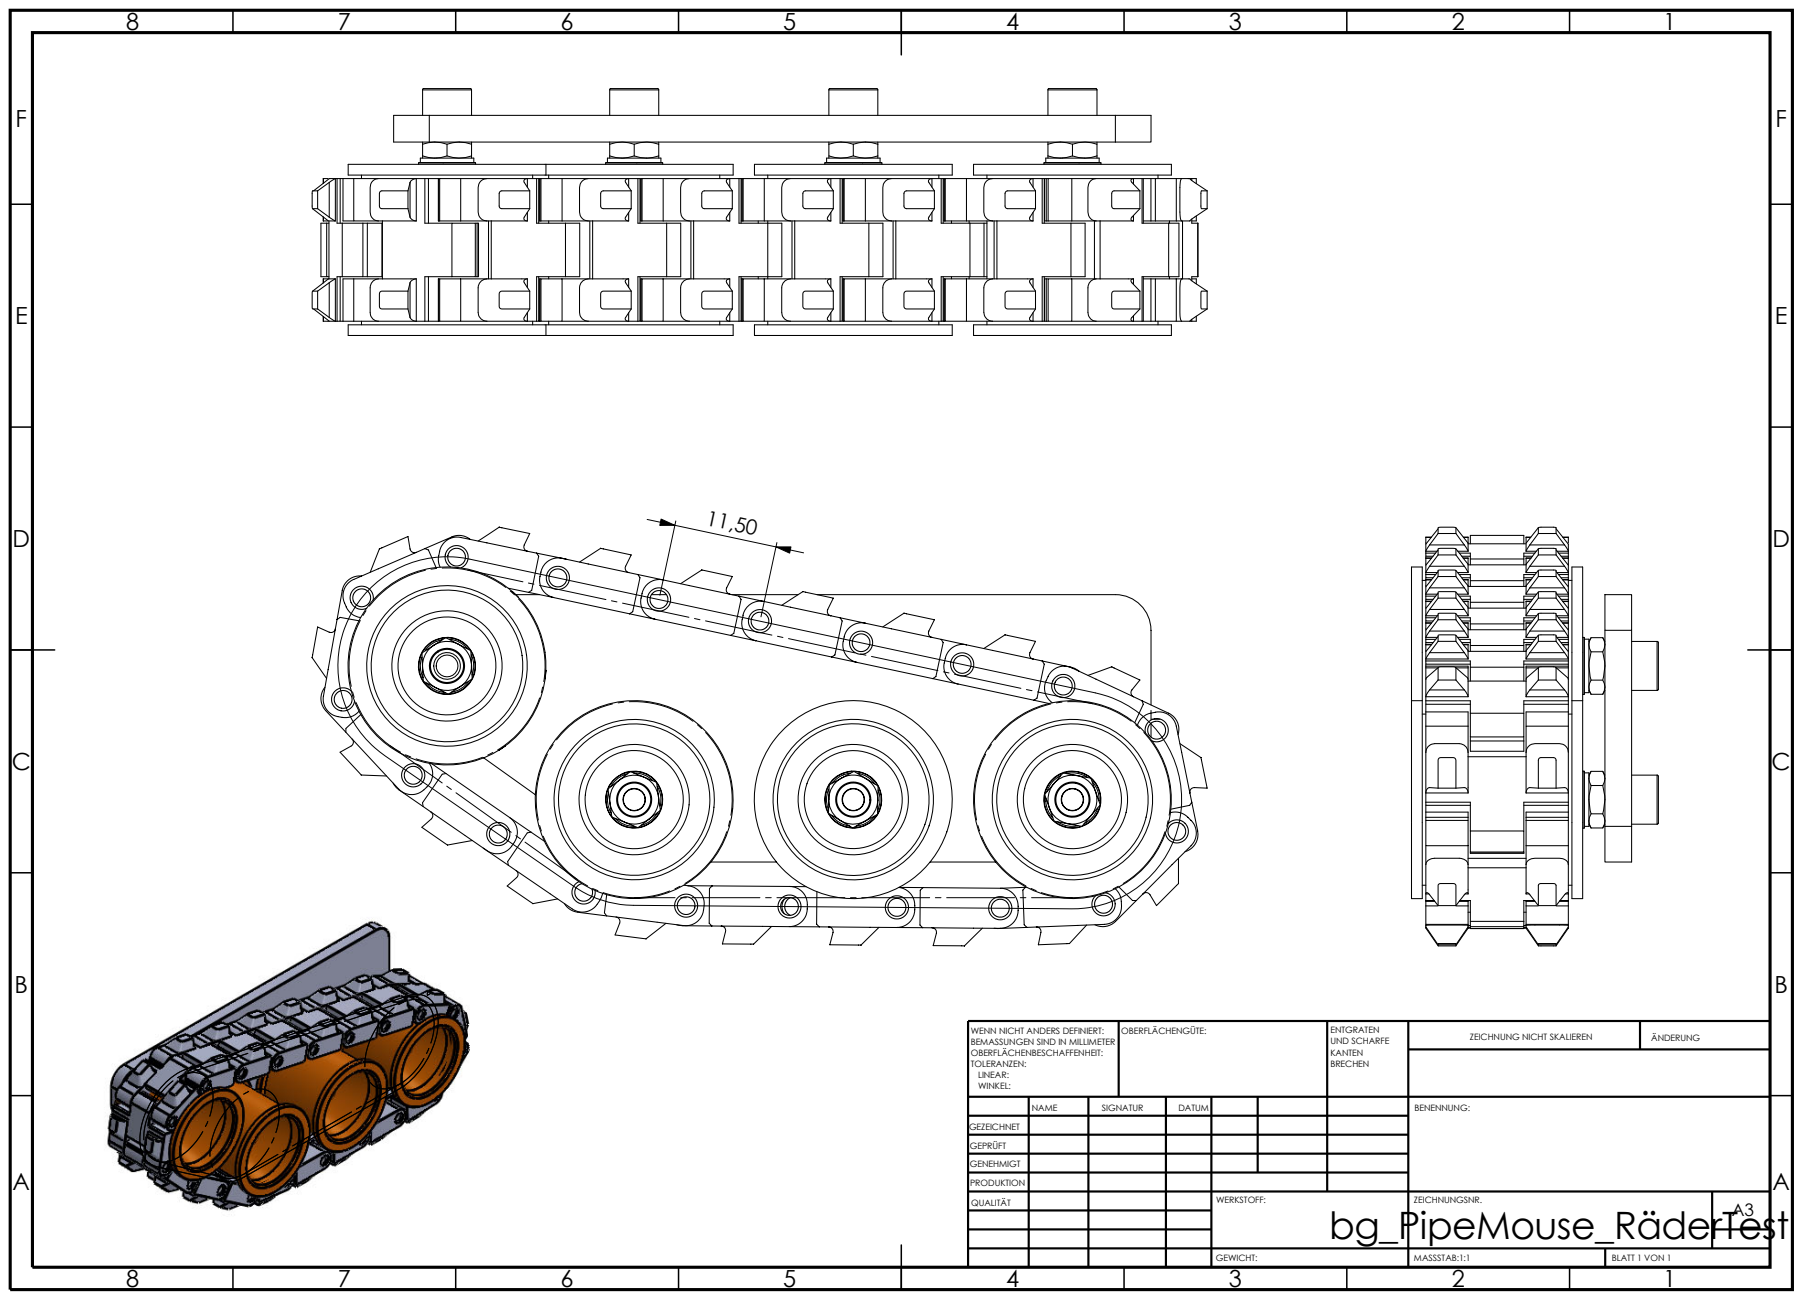
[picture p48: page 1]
bg_PipeMouse_RäderTest; GEWICHT:; MASSSTAB:1:1; BLATT 1 VON 1; ZEICHNUNGSNR.; BENENNUNG:; ZEICHNUNG NICHT SKALIEREN; ÄNDERUNG; WERKSTOFF:; OBERFLÄCHENGÜTE:; BRECHEN; ENTGRATEN; KANTEN; NAME; SIGNATUR; DATUM; UND SCHARFE

WENN NICHT ANDERS DEFINIERT:
BEMASSUNGEN SIND IN MILLIMETER
OBERFLÄCHENBESCHAFFENHEIT:
TOLERANZEN:
LINEAR:
WINKEL:

GEZEICHNET
GEPRÜFT
GENEHMIGT
PRODUKTION QUALITÄT

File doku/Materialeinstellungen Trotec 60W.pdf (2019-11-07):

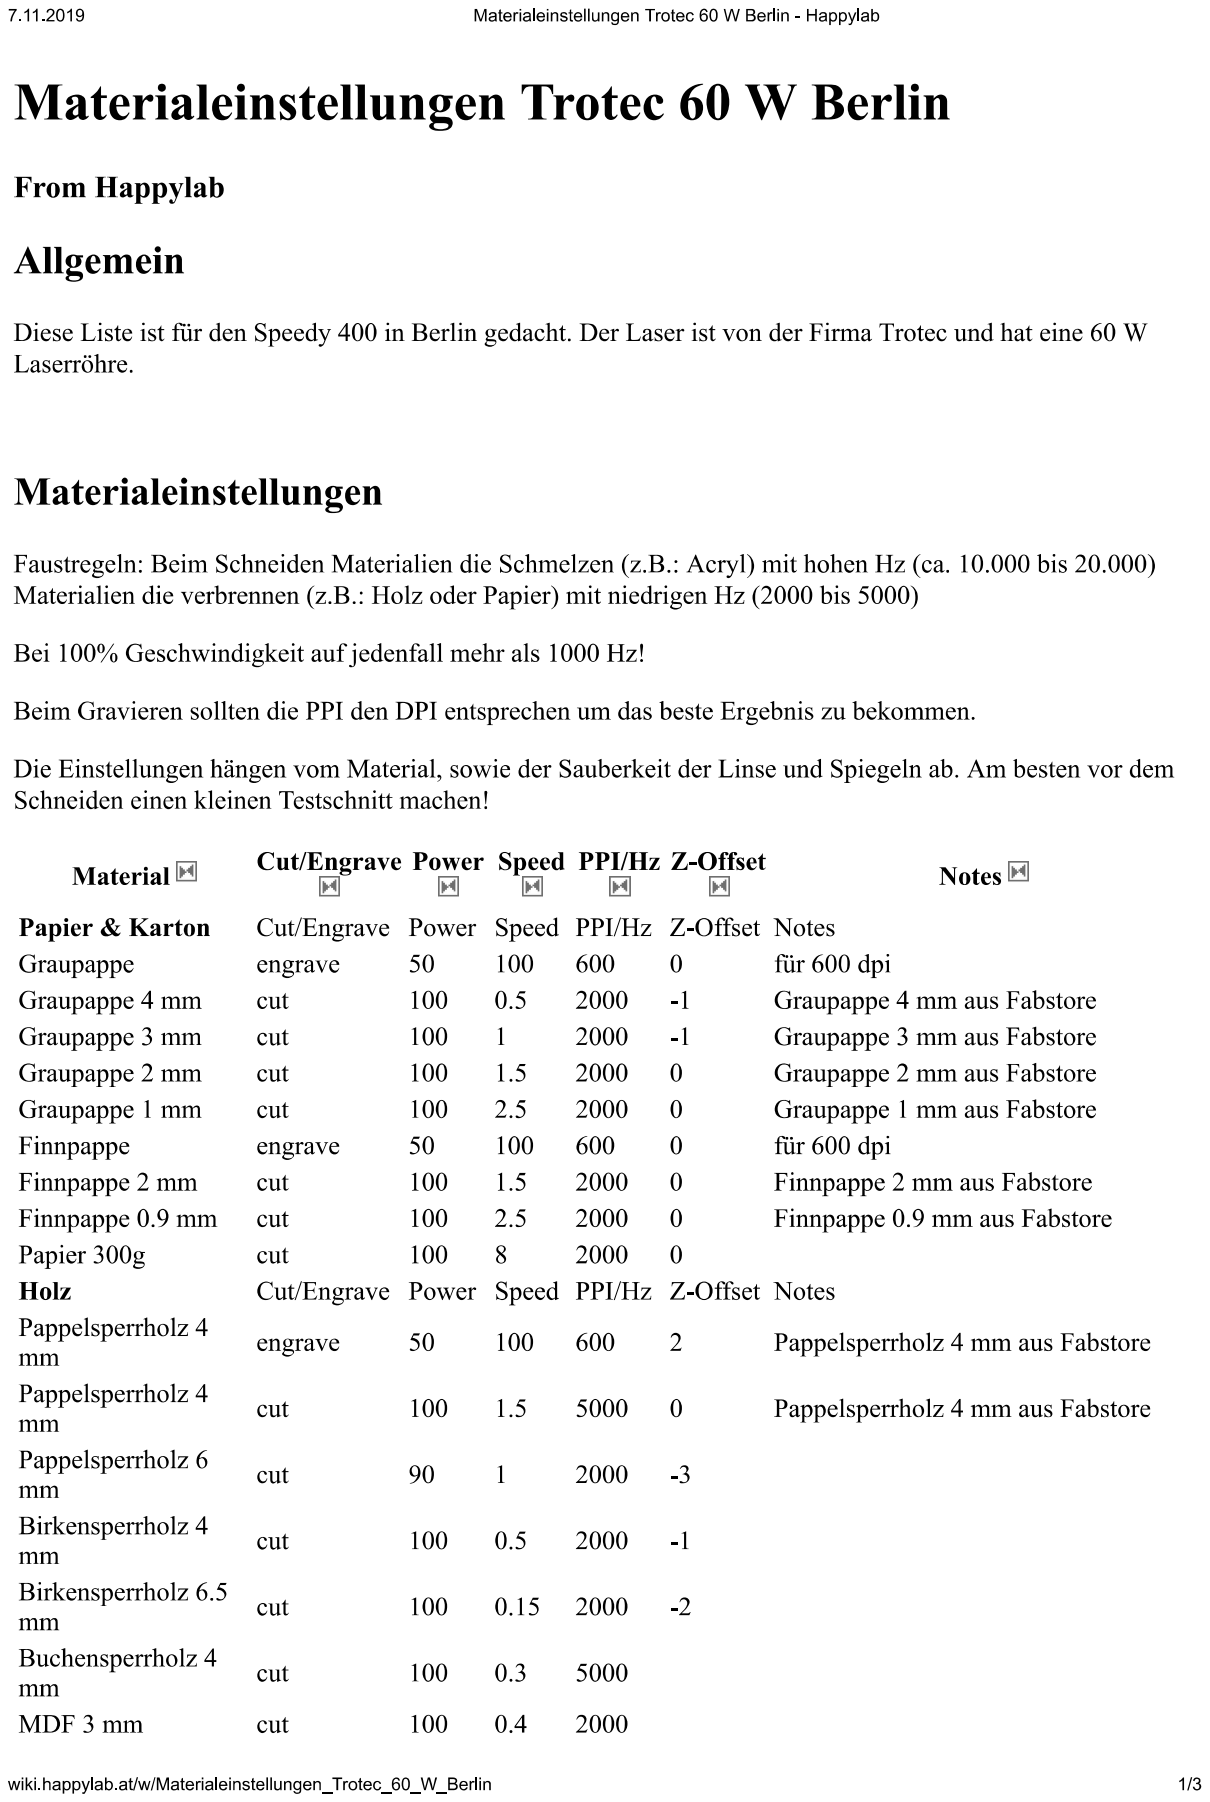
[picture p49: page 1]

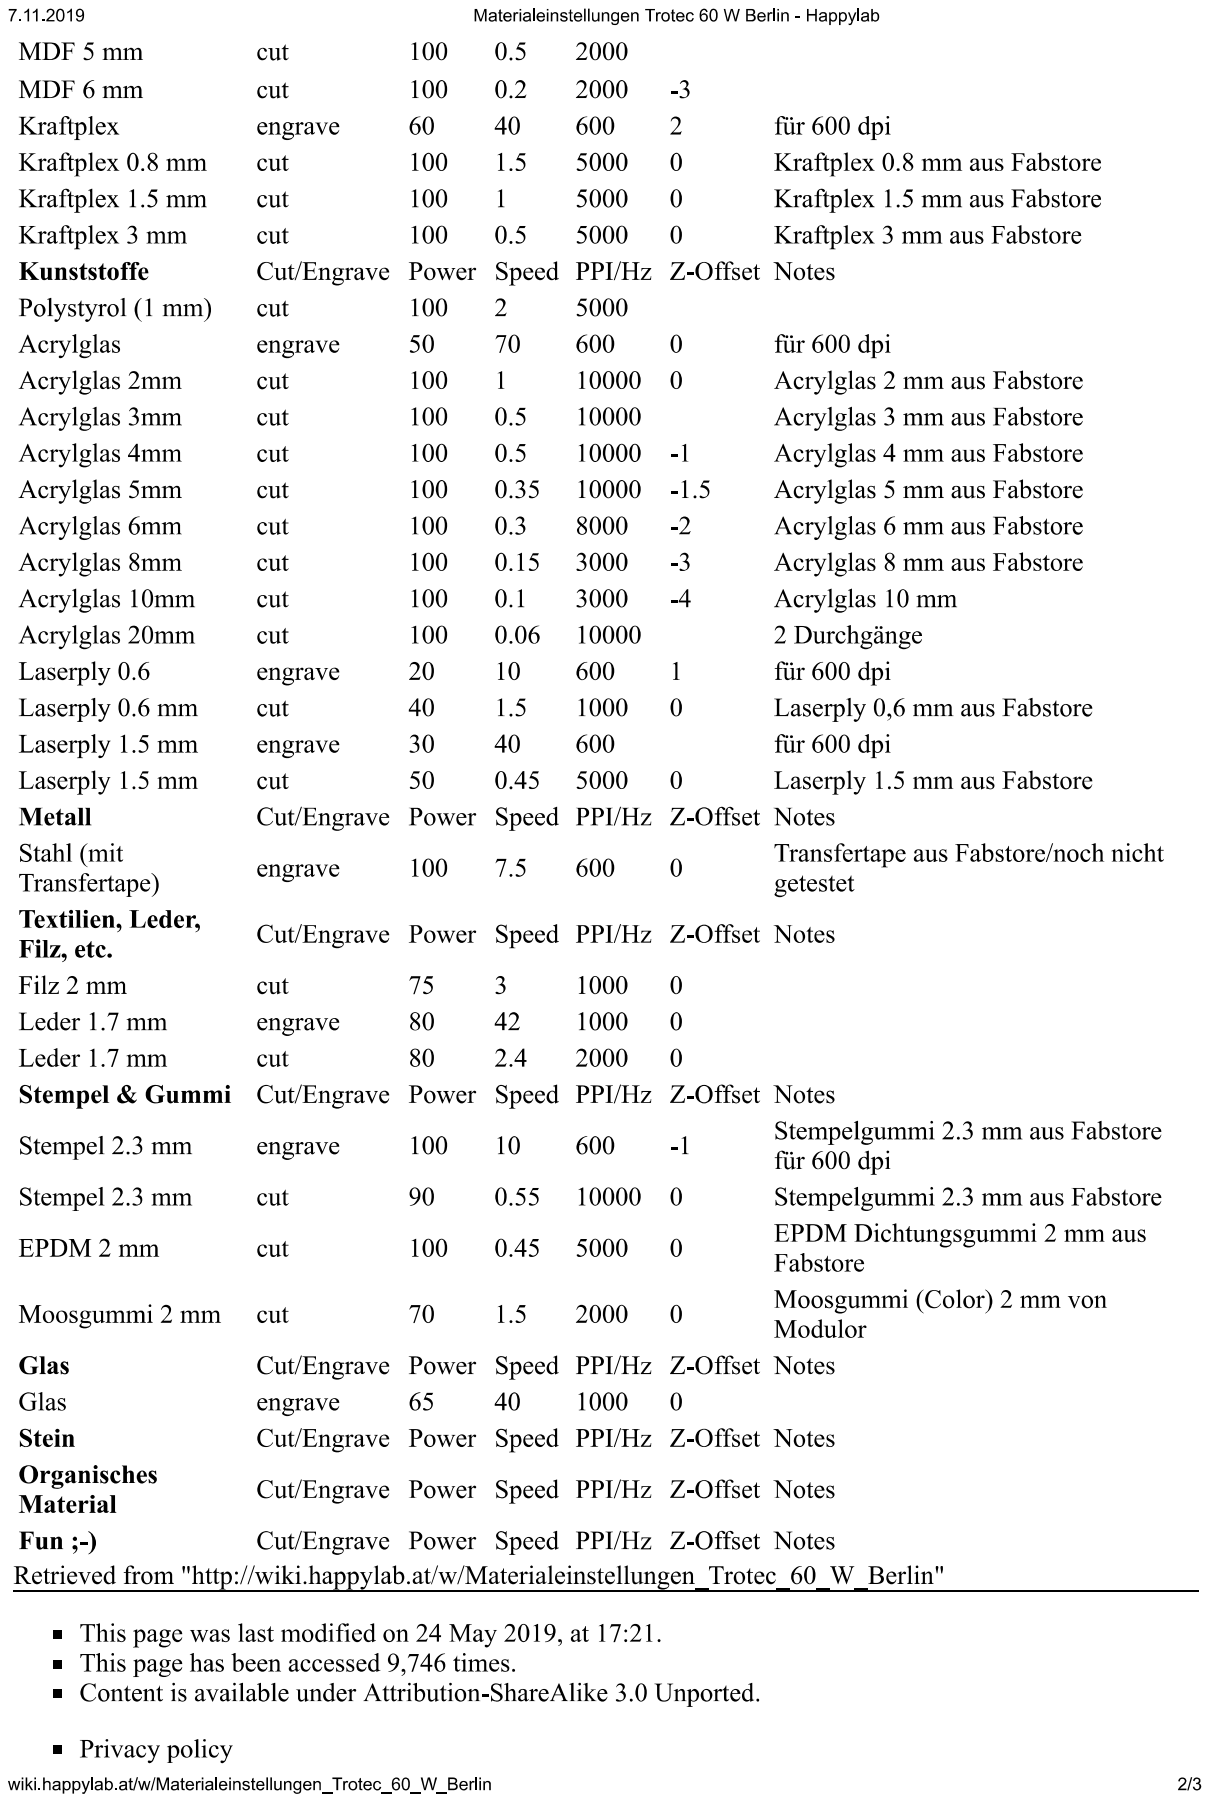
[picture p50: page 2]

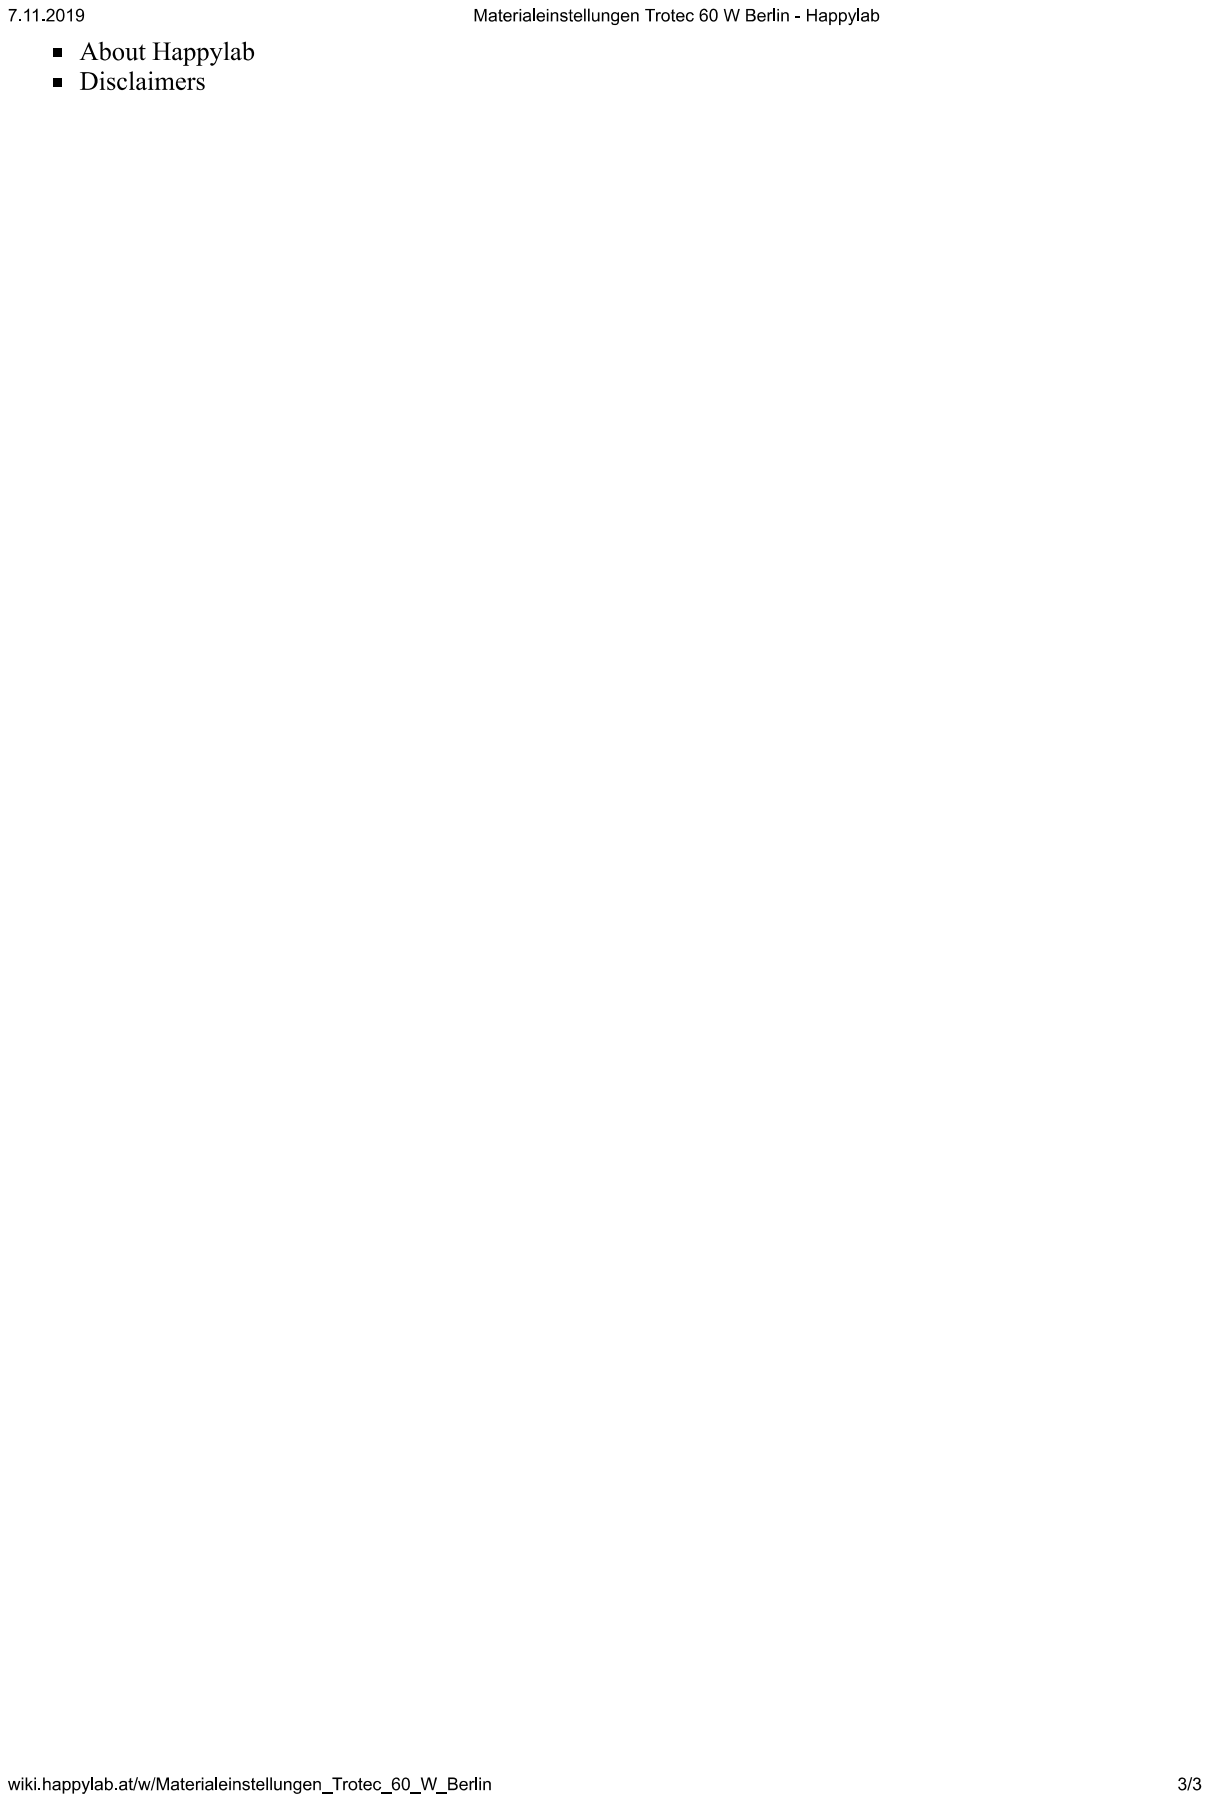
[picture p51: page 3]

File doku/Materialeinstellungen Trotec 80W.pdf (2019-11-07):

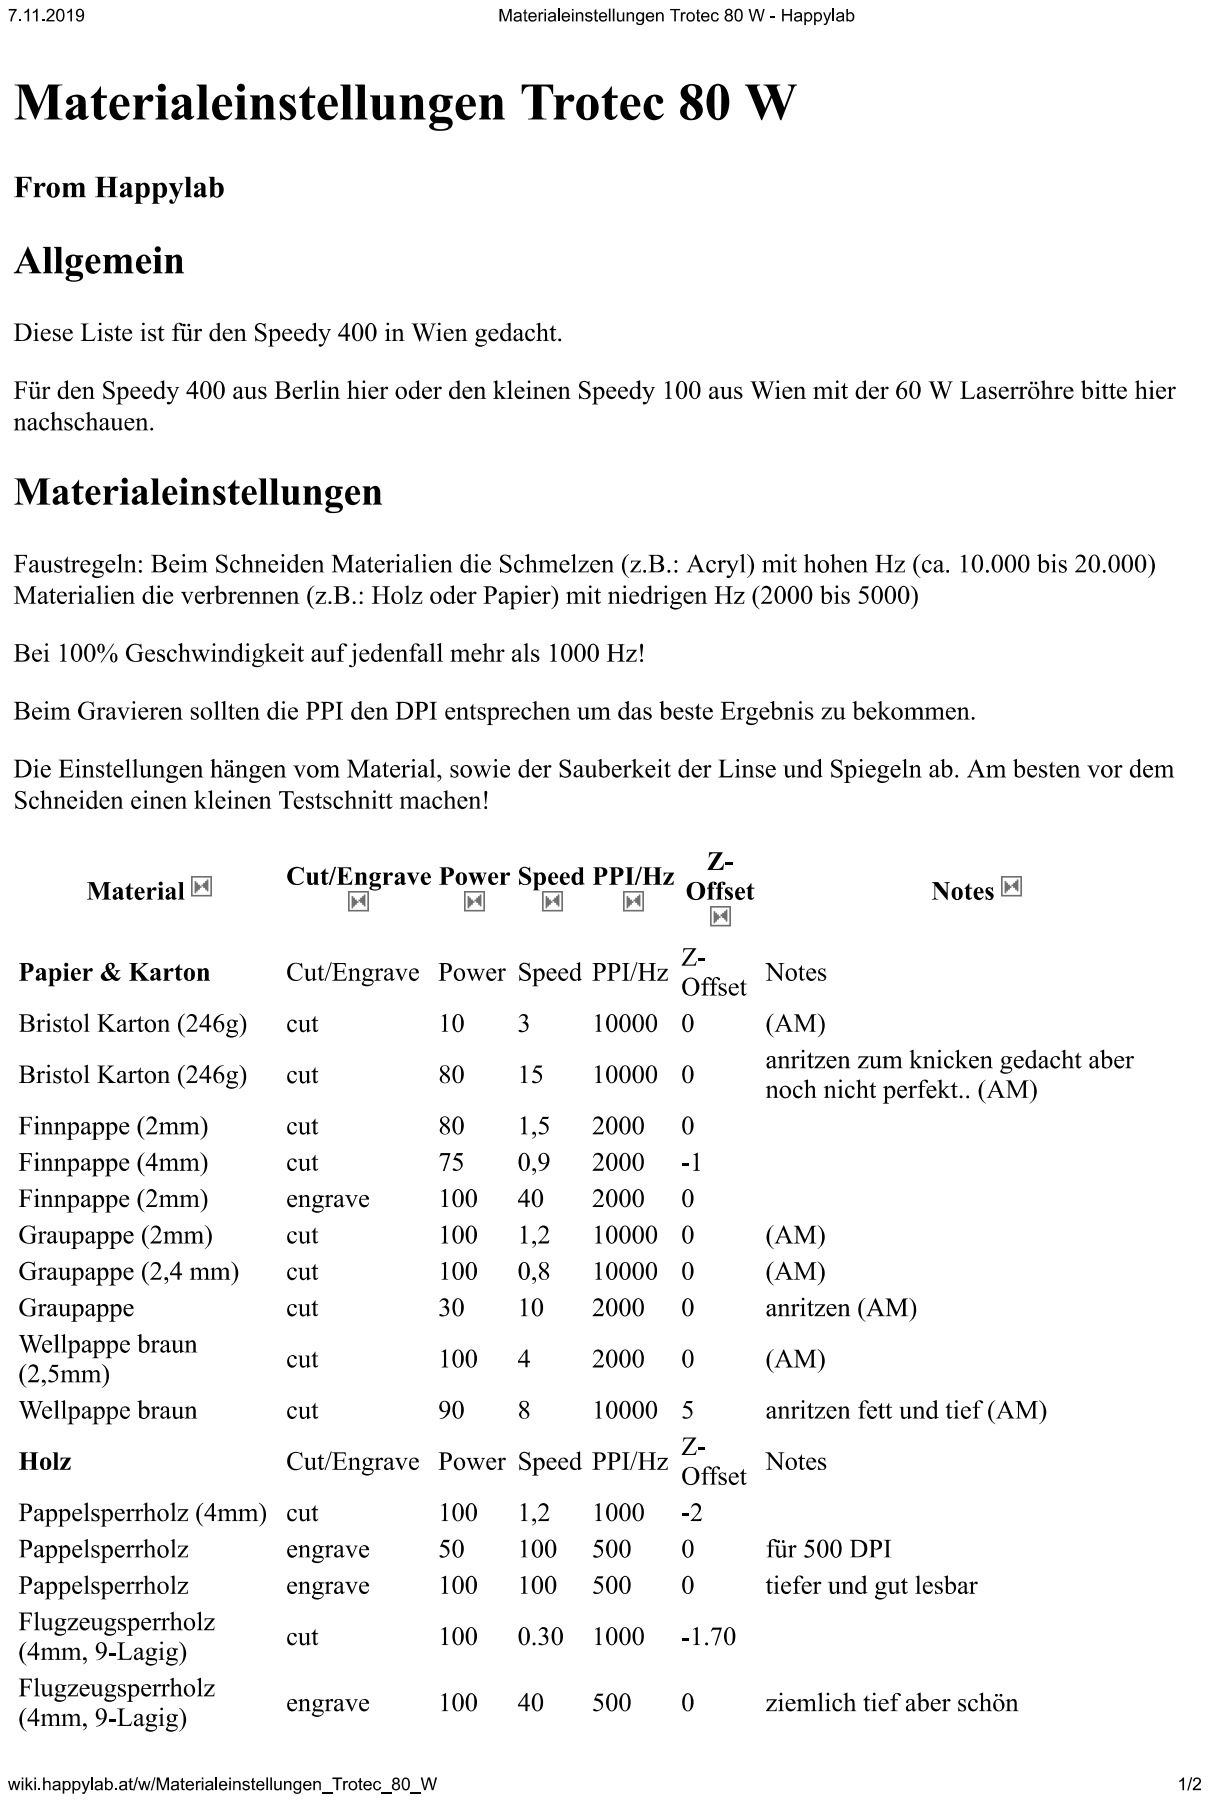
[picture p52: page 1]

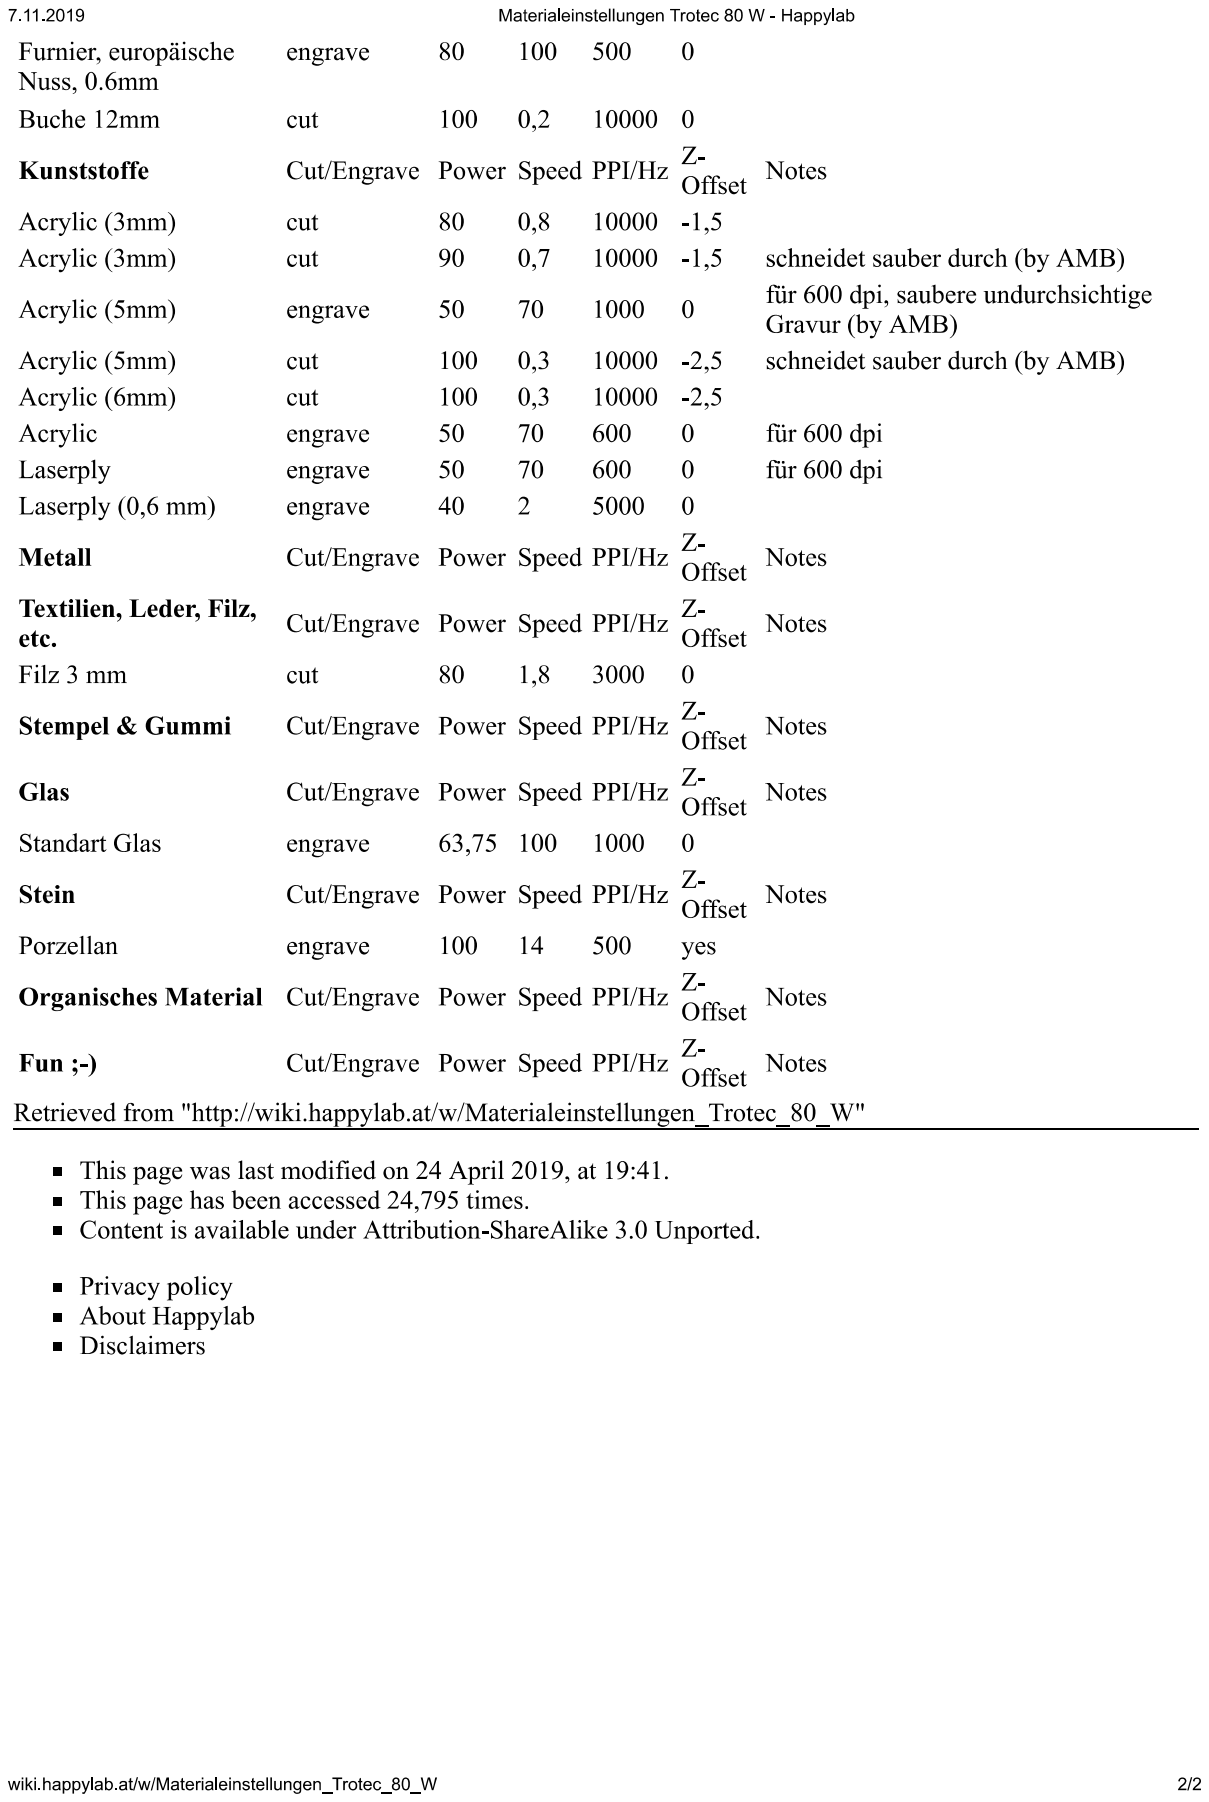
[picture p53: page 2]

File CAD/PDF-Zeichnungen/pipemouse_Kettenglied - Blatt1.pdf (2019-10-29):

E | E
F | F

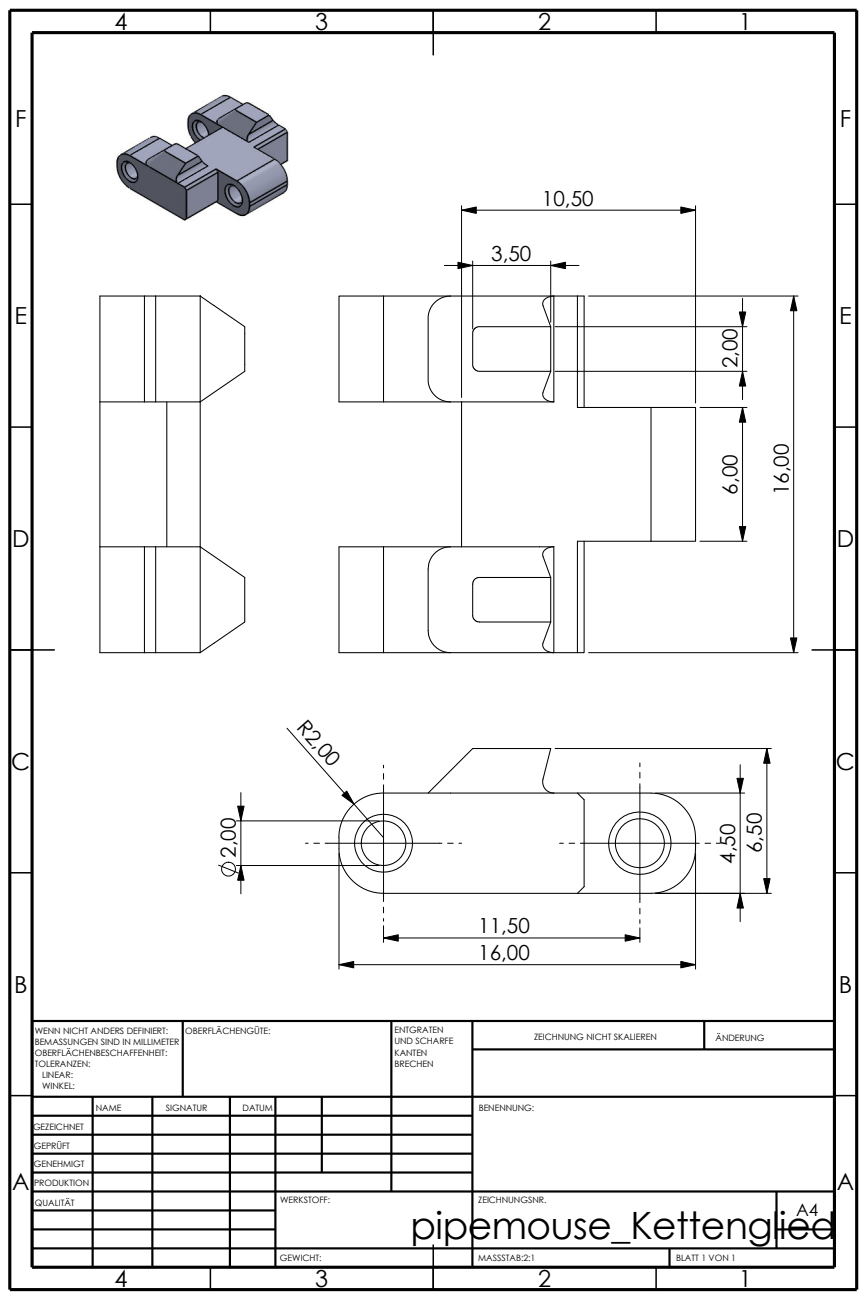
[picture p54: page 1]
MASSSTAB:2:1; BLATT 1 VON 1; ZEICHNUNG NICHT SKALIEREN; ÄNDERUNG; OBERFLÄCHENGÜTE:; BRECHEN; ENTGRATEN; KANTEN; UND SCHARFE

WENN NICHT ANDERS DEFINIERT:
BEMASSUNGEN SIND IN MILLIMETER
OBERFLÄCHENBESCHAFFENHEIT:
TOLERANZEN:
LINEAR:
WINKEL:

NAME | SIGNATUR | DATUM | | | | BENENNUNG:

GEZEICHNET
GEPRÜFT
GENEHMIGT
PRODUKTION
QUALITÄT | | | | WERKSTOFF: pipemouse_Kettenglied GEWICHT: | ZEICHNUNGSNR. | A4

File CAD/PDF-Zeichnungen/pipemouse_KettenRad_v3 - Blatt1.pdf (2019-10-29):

E | E
F | F

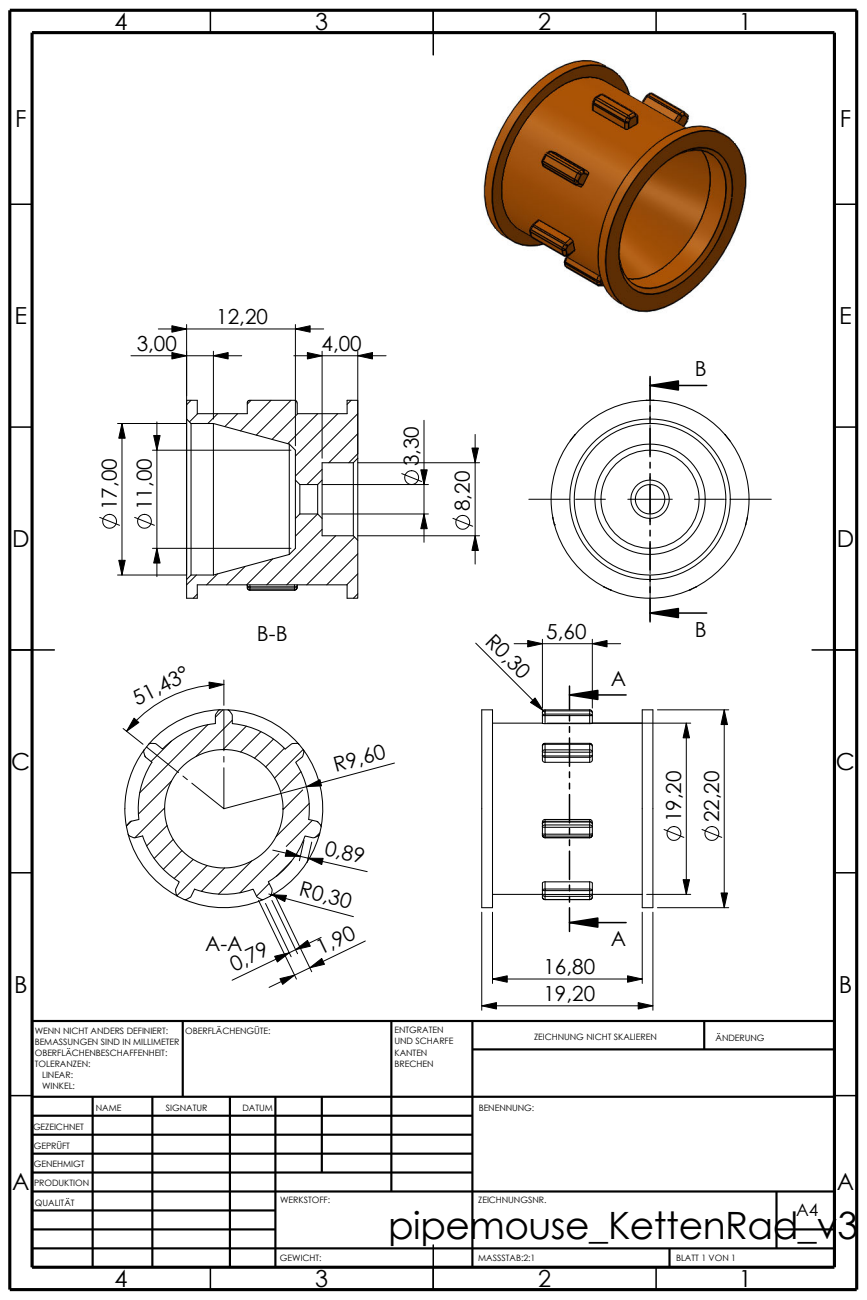
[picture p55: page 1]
MASSSTAB:2:1; BLATT 1 VON 1; ZEICHNUNG NICHT SKALIEREN; ÄNDERUNG; OBERFLÄCHENGÜTE:; KANTEN; UND SCHARFE; ENTGRATEN; BRECHEN

WENN NICHT ANDERS DEFINIERT:
BEMASSUNGEN SIND IN MILLIMETER
OBERFLÄCHENBESCHAFFENHEIT:
TOLERANZEN:
LINEAR:
WINKEL:

NAME | SIGNATUR | DATUM | | | | BENENNUNG:

GEZEICHNET
GEPRÜFT
GENEHMIGT
PRODUKTION
QUALITÄT | | | | WERKSTOFF: pipemouse_KettenRad_v3 GEWICHT: | ZEICHNUNGSNR. | A4

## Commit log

2019-08-30 CAD Ketten und Kettenräder
    erste funtionierende Version der Ketten-Teile
    [pipemouse_KettenRad_v3.SLDPRT, pipemouse_Kettenglied.SLDPRT, pipemouse_Kugellager_8x3x4.SLDPRT]
2019-08-30 Konstruktion Kettenantrieb
    [bg_PipeMouse_Laufrad.SLDASM, bg_PipeMouse_RäderTest.SLDASM, pipemouse_KettenRad_v3.SLDPRT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]
2019-09-02 Kettentest
    Riemenlänge 223,5mm
    [bg_PipeMouse_RäderTest.SLDASM, pipemouse_KettenRäderAbstandsTest.SLDPRT]
2019-10-29 Servo SG90 hinzugefügt, kleine Änderungen...
    [bg_PipeMouse_RäderTest.SLDASM, pipemouse_KettenRäderAbstandsTest.3dm, pipemouse_KettenRäderAbstandsTest.DXF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]
2019-10-29 Zeichnungen für Kette eingefügt
    Zeichnungen mit den wichtigesten Bemaßungen, da Modellen mit SW2019/2020 erstellt und somit nicht mehr in SW18/19 geöffent werden kann.
    Achtung: Baugruppe Kette nur als Beispiel. In der Baugruppe bestehen erhebliche Abweichungen bei den Abständen der Kettenglieder (Fehler in der Kettenglieder-Funktion?)
    [bg_PipeMouse_Laufrad.SLDASM, bg_PipeMouse_RäderTest.SLDASM, bg_PipeMouse_RäderTest.SLDDRW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]
2019-10-30 Recherche: Umbau Servo als Antrieb
2019-11-07 Ketten Tests
    [bg_PipeMouse_Laufrad.SLDASM, bg_PipeMouse_RäderTest.SLDASM, pipemouse_Kettenglied.SLDPRT]
2019-11-07 Simulation Kettenglied mit GummiPlatte
    [bg_PipeMouse_KettenGliedGummi.SLDASM, bg_PipeMouse_SimulationGummiKette.SLDASM, pipemouse_GummiPlatte.SLDPRT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]
2019-11-07 3D Druck Kettenglied GummiPad
    [pipemouse_GummiPlatte.STL, pipemouse_Kettenglied_GummiPad.STL]
2019-11-07 Materialeinstellungen Trotec Laser
2019-11-08 Moosgummi-Pads lasern und einkleben
    [Laser_GummiPad.3dm, pipemouse_GummiPlatte.DXF, pipemouse_GummiPlatte.SLDDRW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]
2019-11-08 Bilder / Videos Lasern Moosgummi-Pads
2019-11-14 3D Druck KettenRad_v3
    mit Abtrieb Servohorn
    [BG_PipeMouse_Servo_SG90.SLDASM, bg_PipeMouse_AntriebsTest.SLDASM, bg_PipeMouse_Antriebsstrang.SLDASM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]
2019-11-14 anpassungen Kettenrad
    [pipemouse_KettenRad_v3.SLDPRT, pipemouse_KettenRad_v3.STL]
2019-12-04 Bodenwanne Anpassungen
    [Lipo_HappyModell_2S_300mAh.SLDPRT, bg_PipeMouse_Antriebsstrang.SLDASM, bg_PipeMouse_Bodenwanne.SLDASM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]
2020-01-07 Anpassungen Servo-Ausschnitt Bodenwanne
    [bg_PipeMouse_Bodenwanne.SLDASM, pipemouse_Bodenwanne.SLDPRT]
2020-01-08 Caddx Kamera Einbau
    [bg_PipeMouse_Bodenwanne.SLDASM, cadxx_Turbo_Eon.SLDPRT, pipemouse_WannenDeckel.SLDPRT]
2020-01-13 Deckel und Kettenspanner
    [Scheibe.SLDPRT, Scheibe.STL, bg_PipeMouse_Bodenwanne.SLDASM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]
2020-01-13 Kettenspanner Anpassungen
    [bg_Kettenspanner.SLDASM, bg_PipeMouse_Bodenwanne.SLDASM, pipemouse_KettenspannRad.SLDPRT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]
